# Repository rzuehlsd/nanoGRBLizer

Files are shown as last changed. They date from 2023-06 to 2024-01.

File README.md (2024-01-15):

# nanoGRBLizer
nanoGRBLizer is a GRBL 1.1 based Arduino Nano controller for Stepcraft SC420 D2 milling machine.
The design is based on the well known GRBLizer controller specifically designed for the Stepcraft mills by Rogier Lodewijks (see https://github.com/eflukx/Stepcraft-GRBLizer). 
The nanoGRBLizer controller uses the open source GRBL1.1h software (https://github.com/gnea/grbl/wiki) and allows in combination with a GRBL code sender (eg. UltimateCNC or UGS) controll of all 3 axes and the spindle of the stepcraft mill. A probe length sens input is also available. 

The functionality of the nanoGRBLizer compared to the original GRBLizer lacks the connections to controll a 4th axis and additional relais. Dimensions and functionalty of the nanoGRBLizer PCB allow for a 1:1 replacement of the WinPCNC USB controller of the Stepcraft mills, which is often used for hobby purposes.

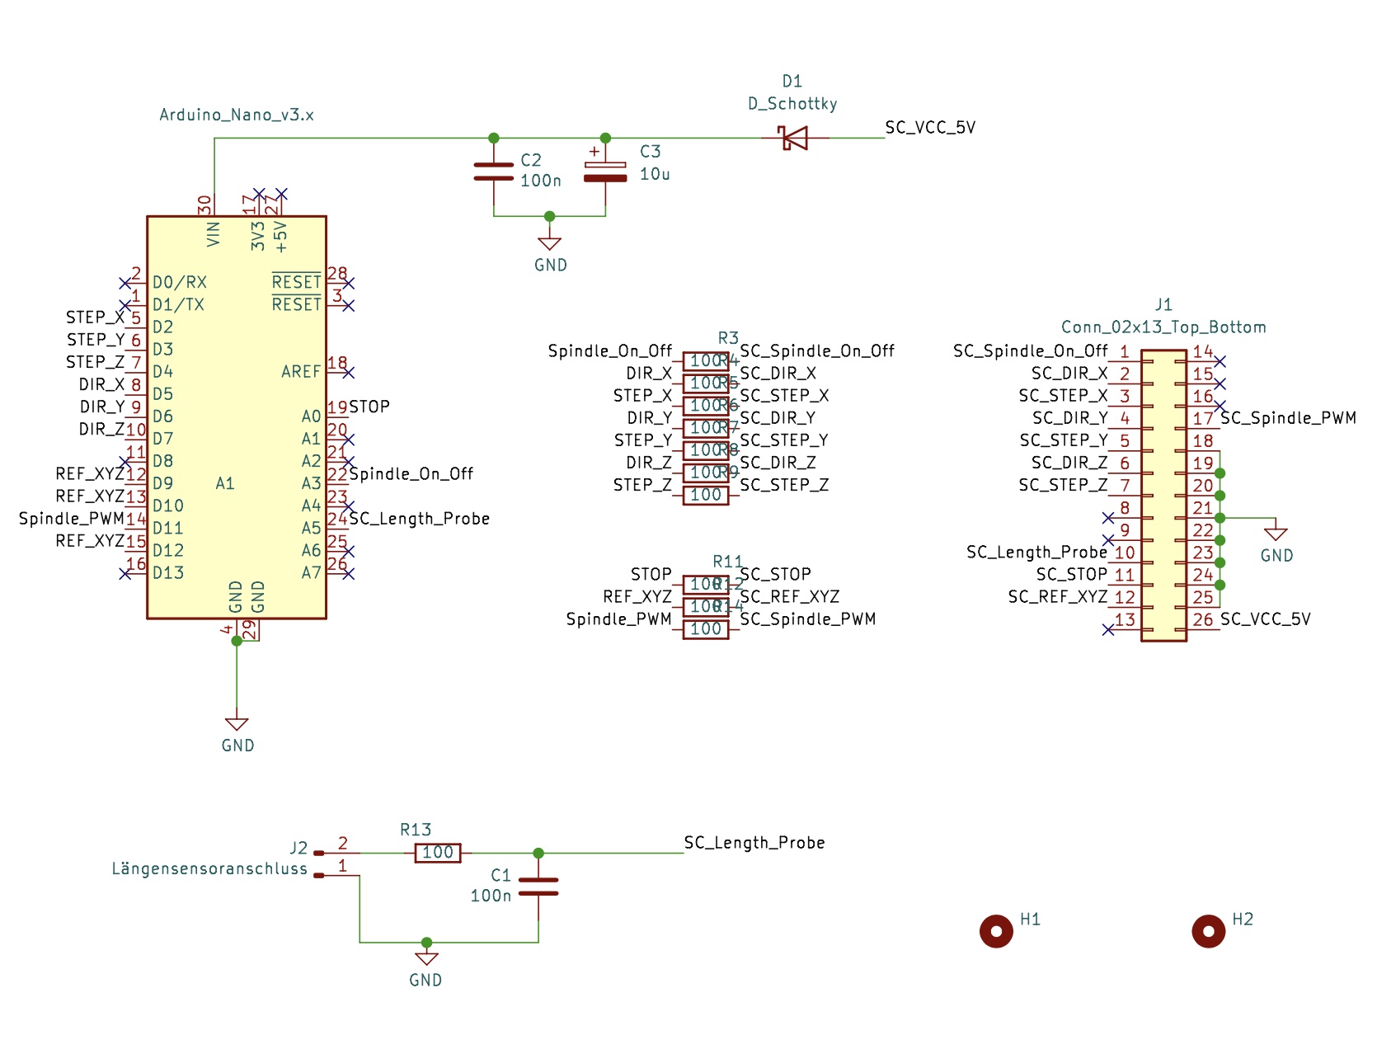
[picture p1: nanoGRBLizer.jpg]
schematic


I first tried the original GRBLizer and ordered a PCB by PCBWay but realized that getting the required parts was problematic and costly. I therefore reduced the original design to the functionalities I really needed and had a specific focus on simplicity and cost. As a result I designed the nanoGRBLizer around a Arduino Nano bord which reduced the complexity a lot and was also very cost efficient. 

This repository holds the KiCAD files to replicate the nanoGRBLizer and gives hints for implementation, configuration and initial operation of the nanoGRBLizer.

## PCB Assembly
There are some caveeats which have to be respected during assembly of the PCB due to the space constraints of the Stepcraft mill.
- First the 6 pin ISP header of the Arduino Nano has to be shorted by about 3mm. Alternatively you have to unsolder the header or insolate it, as the metal shield of the Stepcraft driver board might shorten the pins.
- Directly solder the Arduino Nano on the PCB. Do **not use a socket** as the PCB might not fit into the available space and the USB socket might not be usable.

## Installation of GRBL1.1 firmware
- Download the current version of the GRBL 1.1 software from here: https://github.com/gnea/grbl
- Install the grbl lib according to your Arduino IDE
- Implement the changes to the files cpu_map.h and config.h as described in the next section
- Compile the grbl_uload.ino script from the grbl examples and download to your Nano

## Configuration of Controller
I implemented the grbl settings as described by Rogier in his readme. They did not quite worked for me, but were a very good starting point. 
As I wanted to use the HF500 spindle with my SC420 mill I had to figure out how to get the spindle enable signal on A3 working.
I changed the config.h, the cpu_map.h and the defaults.h file to reflect the changes needed by my configuration. To avoid chnaging configuration settings inside the default configuration for Atmega328 microprocessor I decided to redefine required symbols inside a conditional block directly below the default settings. This redefinitions are guarded by a `#ifdef NANO_GRBLIZER ... #endif` bracket. The symbol NANO_GRBLIZER was then definded in config.h as shown below:
```
// Define CPU pin map and default settings.
// NOTE: OEMs can avoid the need to maintain/update the defaults.h and cpu_map.h files and use only
// one configuration file by placing their specific defaults and pin map at the bottom of this file.
// If doing so, simply comment out these two defines and see instructions below.
#define DEFAULTS_GENERIC
#define CPU_MAP_ATMEGA328P // Arduino Uno CPU
#define NANO_GRBLIZER       // triggers redefinitions in config.h, cpu_map.h and defaults.h for nanoGRBLizer
```
Now add the following code snippet to config.h at the **end of the file**:

```
#ifdef NANO_GRBLIZER

// Paste config redefinitions for nanoGRBLIzer  here:

// do not raise alarm to force initial homing at startup
#undef HOMING_INIT_LOCK // Comment to disable

// Since all limit switches end up being shared on one pin, 
// we can only home one direction at a time.
#define HOMING_CYCLE_0 (1<<Z_AXIS)  // REQUIRED: First move Z to clear workspace.
#define HOMING_CYCLE_1 (1<<Y_AXIS)  // OPTIONAL: Then move X,Y at the same time.
#define HOMING_CYCLE_2 (1<<X_AXIS)  // OPTIONAL: Uncomment and add axes mask to enable

// The stop output of the Stepcraft board is inverted to what GRBL expects.
// However you simply can't swap the switch because the driver board will also
// disable the motors so nothing will move.
#define INVERT_CONTROL_PIN_MASK (1<<CONTROL_RESET_BIT) // Default disabled.

// use safety door open event to stop mill and spindle with emergency stop switch
#define ENABLE_SAFETY_DOOR_INPUT_PIN // Default disabled. Uncomment to enable.

// Allows operation of Stepcraft HF500 spindle via grbl
// Activates definition of spindle on/off signal
#define USE_SPINDLE_DIR_AS_ENABLE_PIN

#endif
```

Now lets change the cpu_map.h file for nanGRBLizer. Past the following code directly below the CPU_MAP_ATMEGA328P definitions into the file.

```
#ifdef NANO_GRBLIZER

// Paste cpu_map.h redefinitions for nanoGRBLizer here.

/* Additional or changed Grbl cpu mappings for nanoGRBLizer v01 with Arduini Nano
   Mill:      Stepcraft sc420 D2
   Spindle:   Stepcraft HF500
*/

// The Stepcraft has all limits on one pin.
#define X_LIMIT_BIT    1  // Uno Digital Pin 9
#define Y_LIMIT_BIT    1  // Uno Digital Pin 9
#define Z_LIMIT_BIT    1  // Uno Digital Pin 9

// redefinition of coolant enable port to save A3 for spindle
#define COOLANT_FLOOD_BIT   6  // Uno Analog Pin 3

// redefinition of safty door bit to be shared with CONTROL_RESET_BIT
// hope this will shutsdown spindle and mill when triggered by E-Stop 
#define CONTROL_SAFETY_DOOR_BIT   0

// redefinition of spindle enable port 
// needs definition of USE_SPINDLE_DIR_AS_ENABLE_PIN in config.h 
// to allow for seperate spindle on/off signal via A3
#define SPINDLE_ENABLE_DDR    DDRC
#define SPINDLE_ENABLE_PORT   PORTC
#define SPINDLE_ENABLE_BIT    3  // Uno Analog Pin 3

#endif //  NANO_GRBLIZER
```

Add the changes to the default parameter definition. Past the following section directly below the `DEFAULTS_GENERIC` block.

```
#ifdef NANO_GRBLIZER

  // Paste changes to generic default settings for nanoGRBLizer with sc420 and HF500 here.

  // My old version of Stepcraft sc420 has spindles with 2mm travel per revolution!
  // At 400 half steps per revolution this leads to 200.000 half steps per millimeter
  // whereas the newer versions have spindles with 3mm travel per revolution, hence
  // 133.333 half steps per mm travel!

  #define DEFAULT_X_STEPS_PER_MM 200.000		// standard will be 133.333
  #define DEFAULT_Y_STEPS_PER_MM 200.000		// standard will be 133.333
  #define DEFAULT_Z_STEPS_PER_MM 200.000		// standard will be 133.333
  #define DEFAULT_X_MAX_RATE 800.0 // mm/min
  #define DEFAULT_Y_MAX_RATE 800.0 // mm/min
  #define DEFAULT_Z_MAX_RATE 800.0 // mm/min
  #define DEFAULT_X_MAX_TRAVEL 300.0 // mm NOTE: Must be a positive value.
  #define DEFAULT_Y_MAX_TRAVEL 420.0 // mm NOTE: Must be a positive value.
  #define DEFAULT_Z_MAX_TRAVEL 80.0 // mm NOTE: Must be a positive value.
  #define DEFAULT_SPINDLE_RPM_MAX 20000.0 // rpm
  #define DEFAULT_SPINDLE_RPM_MIN 3000.0 // rpm
  #define DEFAULT_STEP_PULSE_MICROSECONDS 50
  #define DEFAULT_STEPPER_IDLE_LOCK_TIME 100 // msec (0-254, 255 keeps steppers enabled)
  #define DEFAULT_INVERT_ST_ENABLE 1 // false
  #define DEFAULT_INVERT_LIMIT_PINS 1 // false
  #define DEFAULT_SOFT_LIMIT_ENABLE 0 // false
  #define DEFAULT_HARD_LIMIT_ENABLE 1  // false
  #define DEFAULT_INVERT_PROBE_PIN 0 // false
  #define DEFAULT_HOMING_ENABLE 1  // false
  #define DEFAULT_HOMING_DIR_MASK 1 // move x to left to find limit switch
  #define DEFAULT_HOMING_FEED_RATE 120.0 // mm/min
  #define DEFAULT_HOMING_SEEK_RATE 900.0 // mm/min
  #define DEFAULT_HOMING_DEBOUNCE_DELAY 250 // msec (0-65k)
  #define DEFAULT_HOMING_PULLOFF 1.0 // mm

#endif
```

## Initial Operation with UltimateCNC and nanoGRBLizer V1.0
I used UltimateCNC on Linux as a gcode sender and after initial connection to the nanoGRBLizer a error alarm showed up, which confused me a lot. After a few hours of debugging and head scratching I found the solution in the config.h file of the grbl library. I just disabled the HOMING_INIT_LOCK and could proceed. Homing and moving of all axes was fine, but I had a problem with the z-probing. I connected a simple probe at the probe connector of the nanGRBLizer and tried probing. I had to hit the stop switch as the bit did not stop at contact with my metal sheet. 

Measurements showed that the voltage between both pins of the probe dropped from about 5V to OV but the probe event was not triggered. Testing outside the SC420 showed normal behaviour, eg. a probe event was recognized without problems. So the problem has to be the combination of nanoGRBLizer and SC420. After I connected the probe directly to the probe connector on the stepcraft mainboard everything worked as expected! Well now I understand the optional jumper to break the connection between A5 and SC_Length in the original GRBLizer schematic.

There was just one additional change I had to make to the UltimateCNC default probe macro. The probe connected to the metal sheet and immediatldiatly raised an alarm. A closer look at the probe macro showed that after initial contact an additional G38.2 command was issued without raising the spindle.
I changed that to `G38.2 Z-50 F50; G92 Z0; G0 Z10` as a first fix and all was fine.

Further testing showed that all 3 axes did not travel the required distances. After some test and head scratching I figured out (sometimes its worth looking into the manual) that my early type of SC420 has spindles with 2mm travel distance per revolution and 200 steps per revolution stepper motors. As the Stepcraft drivers work in half step mode we have 400 half steps per revolution. After adjusting the (half) steps per mm travel to 200.000 for all axes ($100, $101 and $102) everything worked as expected.

So if you try to use this controller I hope the information above will help you. Have fun!

## IMPORTANT NOTE  - Changes to nanoGRBLizer Rev 1.1

When I tried to use AutoLevelling in UGS/UltimatCNC I discovered a very strange behavior. After initial x axis zero AutoLevellimng could bestartet but stopped at firs probe position with an error (incompatible initial state for probing). After some tests I found the reason to be the probe connected to the Stepcraft mainboard.
After I interrupted the connection to  J1 pin 10 (Stepcraft probe sense connection) and connected the probe to J1 on the nanoGRBLizer controller everything worked as expected.

These changes to the schematic and the board layout are reflected in the nanoGRBLizer Rev 1.1

In Addition I included the files for grbl V1.1h with all SC 420 D2 related changes to the config.g, cpu_map.h and defaults.h files. So just compile and upload grblUpload.ino and you are done. All relevant settings for Stepcraft SC 420 D2 are included in the code.

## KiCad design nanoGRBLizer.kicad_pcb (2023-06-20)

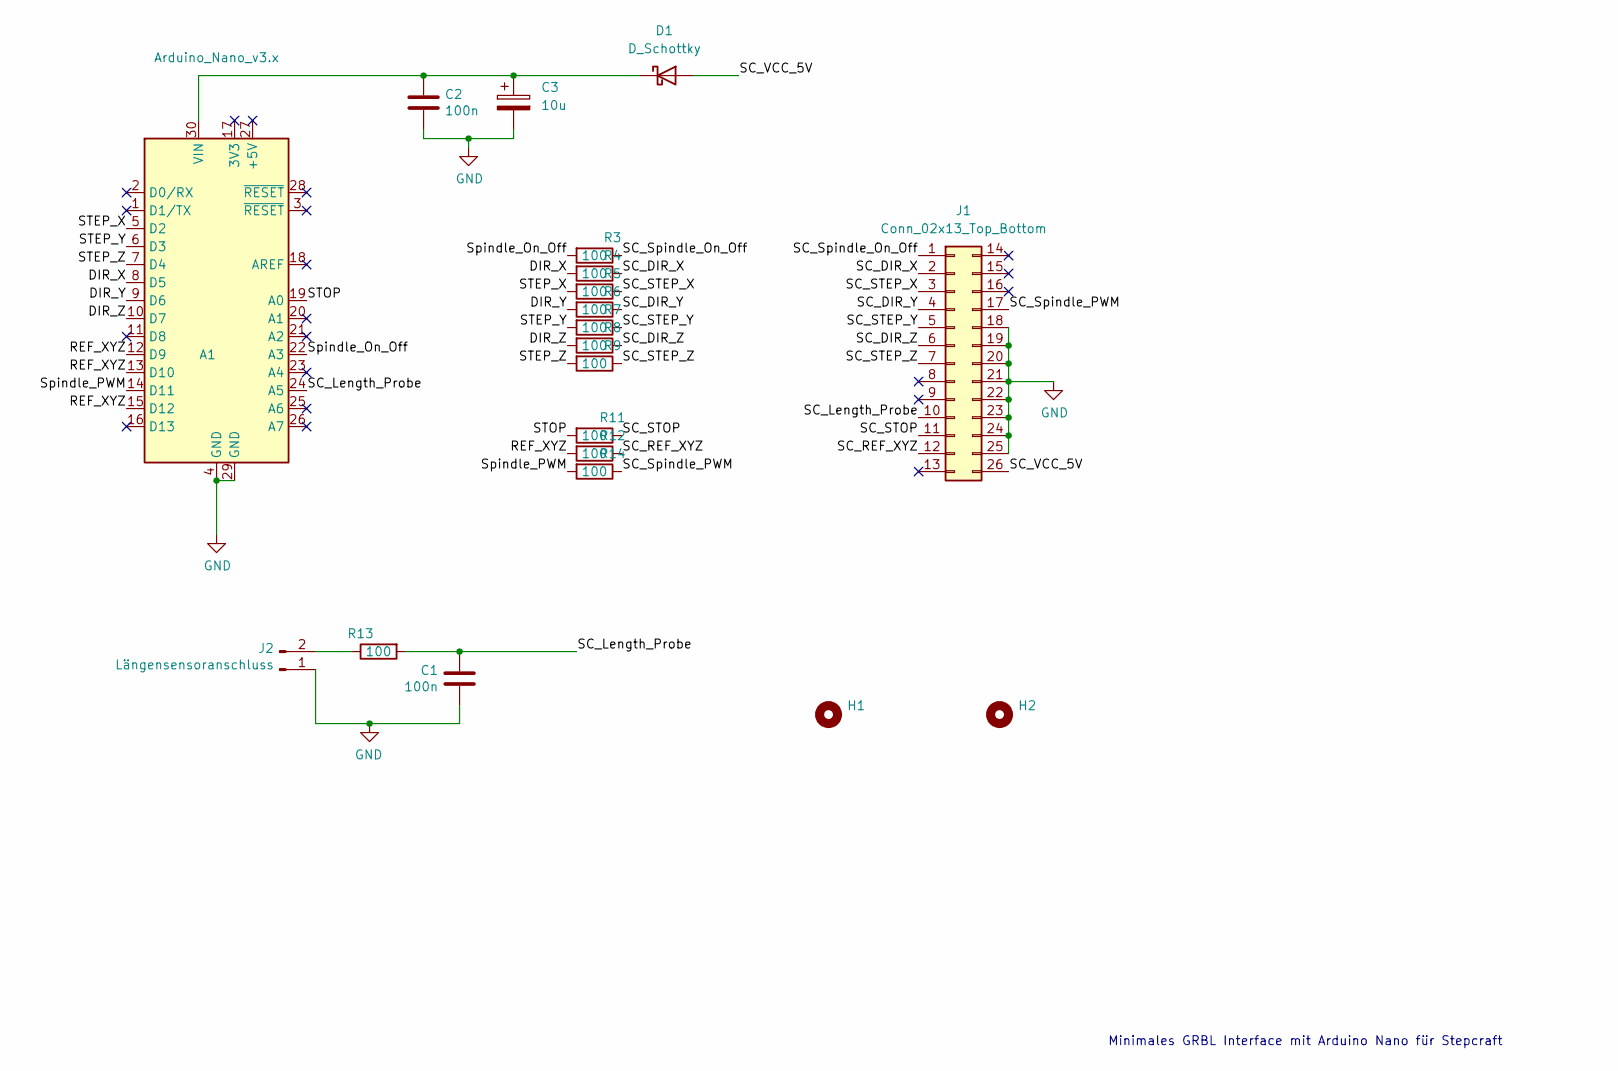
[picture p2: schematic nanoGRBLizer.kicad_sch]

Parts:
A1: Arduino_Nano_v3.x; Arduino_Nano
C1, C2: 100n; C_Axial_L3.8mm_D2.6mm_P7.50mm_Horizontal
C3: 10u; CP_Radial_D8.0mm_P2.50mm
D1: D_Schottky; D_DO-15_P10.16mm_Horizontal
H1, H2: MountingHole; MountingHole_3.2mm_M3
J1: Conn_02x13_Top_Bottom; PinHeader_2x13_P2.54mm_Horizontal_top_bootom
J2: Längensensoranschluss; Molex_SL_171971-0002_1x02_P2.54mm_Vertical
R3, R4, R5, R6, R7, R8, R9, R11, R12, R13, R14: 100; R_Axial_DIN0207_L6.3mm_D2.5mm_P10.16mm_Horizontal

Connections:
/DIR_X: A1.8 (D5), R4.2
/DIR_Y: A1.9 (D6), R6.2
/DIR_Z: A1.10 (D7), R8.2
/REF_XYZ: A1.12 (D9), A1.13 (D10), A1.15 (D12), R12.2
/SC_DIR_X: J1.2, R4.1
/SC_DIR_Y: J1.4, R6.1
/SC_DIR_Z: J1.6, R8.1
/SC_Length_Probe: A1.24 (A5), C1.1, J1.10, R13.2
/SC_REF_XYZ: J1.12, R12.1
/SC_STEP_X: J1.3, R5.1
/SC_STEP_Y: J1.5, R7.1
/SC_STEP_Z: J1.7, R9.1
/SC_STOP: J1.11, R11.1
/SC_Spindle_On_Off: J1.1, R3.1
/SC_Spindle_PWM: J1.17, R14.1
/SC_VCC_5V: D1.2 (A), J1.26
/STEP_X: A1.5 (D2), R5.2
/STEP_Y: A1.6 (D3), R7.2
/STEP_Z: A1.7 (D4), R9.2
/STOP: A1.19 (A0), R11.2
/Spindle_On_Off: A1.22 (A3), R3.2
/Spindle_PWM: A1.14 (D11), R14.2
GND: A1.4 (GND), A1.29 (GND), C1.2, C2.2, C3.2, J1.18, J1.19, J1.20, J1.21, J1.22, J1.23, J1.24, J1.25, J2.1
unnamed: A1.30 (VIN), C2.1, C3.1, D1.1 (K)
unnamed: J2.2, R13.1

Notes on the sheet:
Minimales GRBL Interface mit Arduino Nano für Stepcraft

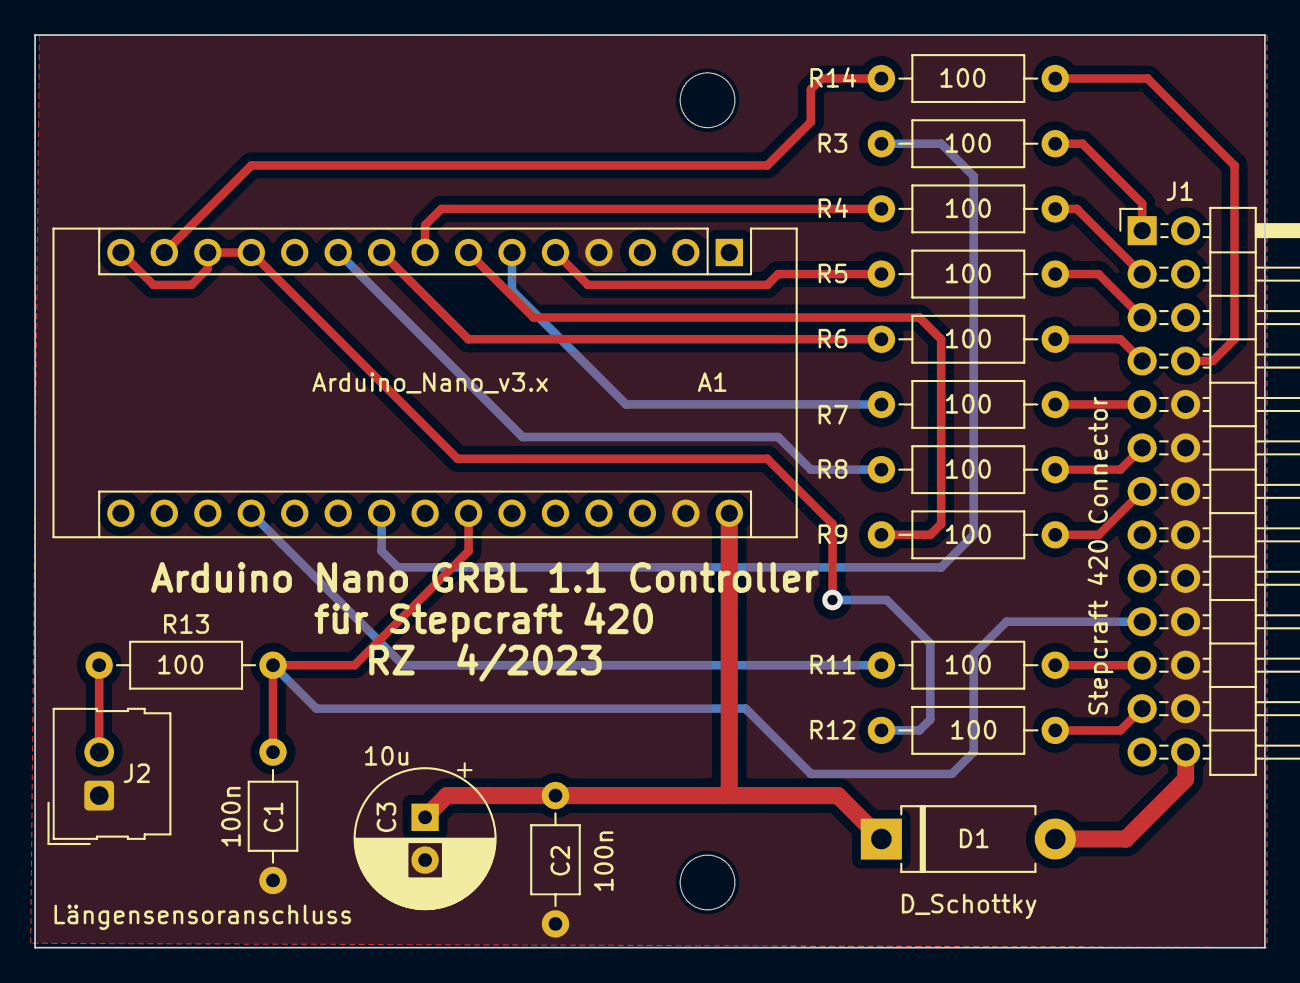
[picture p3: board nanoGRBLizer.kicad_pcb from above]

Board: 2 copper layers, 71.9 x 53.3 mm, 20 parts (0 on the bottom side), 25 nets.

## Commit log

2023-07-11 Add files via upload
    Changes to Dokumentation due to different settings for spindle travel per revolution
2023-07-11 Add files via upload
    Changes to GRBL parameters for $100, $101 and $102
